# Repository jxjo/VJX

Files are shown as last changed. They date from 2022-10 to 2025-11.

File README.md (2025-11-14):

<sup>Project renamed from V-JX to VJX in December 2022 </sup>

# Project VJX
A fast glider for slopes and F3F competition. 

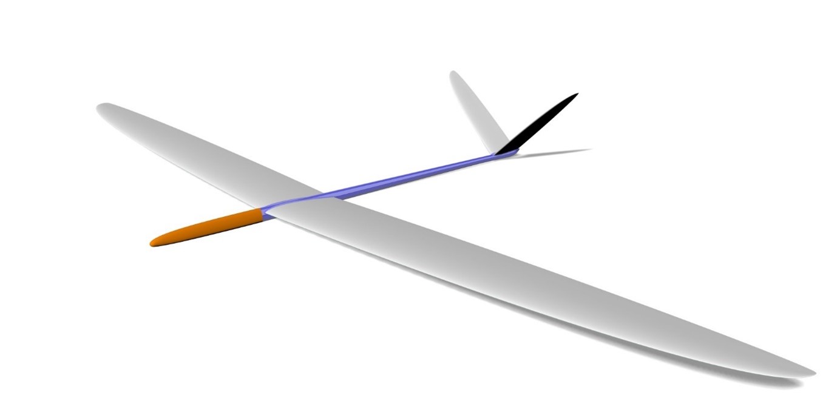
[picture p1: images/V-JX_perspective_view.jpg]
VJX VJX perspective view


VJX is a common project of Jochen Guenzel and Mario Perner where Jochen focuses on aerodynamic design and Mario on engineering and building of the model. 

Within this repository, we want to make a "full stack description" - i.e. from the aerodynamic design to the final build out of molds. As far as possible, we will make the calculations and plans available "open source" and thus also invite to a lively discussion, in which we all will hopefully be a bit smarter in the end.

#### Update 2024

A new wing, called [VJX.glide](wing.glide/README.md), is designed which complements the original VJX for medium to low conditions.

#### Update 2025

The original VJX wing has been revised and a little bit tamed to achieve better high lift capabilities. The new wing is called [VJX.race](wing.race/README.md). 

Have a look at [VJX Project Overview](#vjx-project-overview) for more information about the different developments and their current state. 

## Chapters

#### [Preliminary remarks on the procedure](#preliminary-remarks-on-the-procedure)

#### [Wing](wing/design/wing_design_1.md)
* [Design - Airfoil sections, planform, control surfaces](wing/design/wing_design_1.md) 
* [CAD](https://www.rc-network.de/threads/projekt-v-jx.11886149/post-12199653) - on RCN (de)
* [Molds and Build](https://www.rc-network.de/threads/projekt-v-jx.11886149/post-12201770) - on RCN (de)

#### [Wing VJX.glide](wing.glide/README.md)
#### [Wing VJX.race](wing.race/README.md)

####	[Tail](tail/tail_design.md)
* [Design - Tail, rudder](tail/tail_design.md) 
* [CAD and Molds](https://www.rc-network.de/threads/projekt-v-jx.11886149/post-12285083) - on RCN (de)

#### [Fuselage](fuselage/fuselage_design.md) 
* [Design - Outline, CAD](fuselage/fuselage_design.md) 
* [Molds](https://www.rc-network.de/threads/projekt-v-jx.11886149/post-12289032) - on RCN (de)

#### [Flight Experiences](#flight-experience)
#### [Project Overview](#vjx-project-overview)
#### [History](#project-history)
#### [Acknowledgement](#acknowledgements)

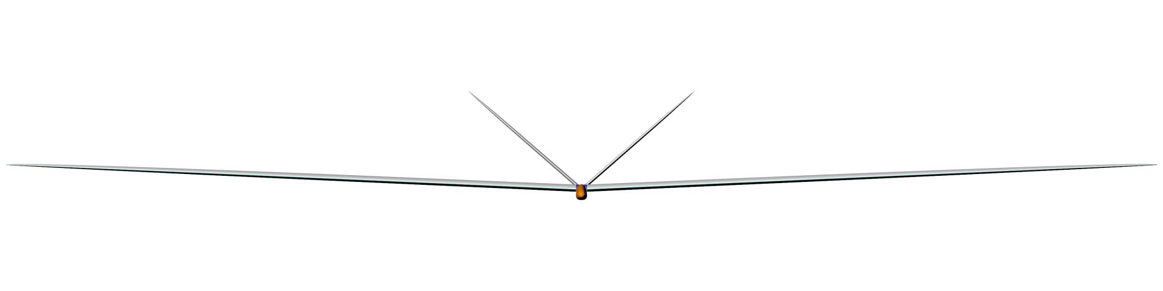
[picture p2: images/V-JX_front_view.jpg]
VJX VJX perspective view

## Preliminary remarks on the procedure

The approach with VJX is somehow atypical for the design of a new model. 

It all started with the [JX-GS airfoil family](https://github.com/jxjo/Airfoils/tree/main/JX-GS)   , which was developed specifically for F3F, but was not based on a specific model design.  In the course of time, however, thoughts matured as to what an optimal wing for this airfoil family should look like.  Which eventually resulted in a first wing design. 

Since a "proof of concept" of this wing design should be carried out as early as possible, the complete design of a new model was out of the question.   With a "test vehicle", the new wing should be put into the air as quickly as possible in order to test its performance. 

We opted for the ["Vantage"](https://ccm.in.ua/en/catalog/r-c-models/vantage/), Mario's current design for F3F/F3B.

The Vantage has perfect dimensions of a current F3F model, which makes the fuselage and tail very well suited to be equipped with a new wing module to evaluate the characteristics of VJX - also in comparison. 

In the development of a new plane, such a separate consideration of the individual components wing, tail and fuselage can be dangerous. The mutual interaction is too complex to achieve an optimized overall design. On the other hand, over the past 30 years, with countless great designs, a narrow design corridor has emerged as to what an optimal model for the F3F flight task should look like. 

Even if it may not be possible to achieve the last bit of improvement by looking at the main components separately, the procedure in the sense of "separation of concerns" of the individual components simplifies the overall development immensely.  As long as you move in the described design corridor, the probability of a "wrong design" is relatively low...

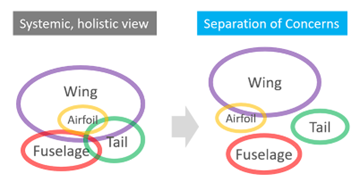
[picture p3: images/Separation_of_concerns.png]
Separation of concerns


A further aspect or guideline for the aerodynamic design, including the profile structure, was: Wherever possible and sensible, a more defensive solution with a "wide optimum" was given preference over exhaustion in a narrow area. 

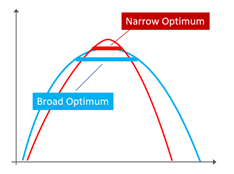
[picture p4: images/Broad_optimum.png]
Broad optimum


The danger of not hitting the "sweet spot" of a narrow optimum under competition flight conditions and thus having to accept significant performance losses far outweighs the prospect of minimal profits compared to a solution with a broad optimum.   

### Design Goals of VJX

"Pretty daring" you could say. To get involved in the round of excellent and mature F3F models such as the Freestylers, Pitbulls, Shintos, Vantage and the numerous other top models. To be even "better" in the end!

The key is certainly that there can no longer be a one-dimensional "better" in the current top models. Each model is practically unbeatable on its own. 

The difference lies in the specific characteristics of the models, which in their sum are decisive for whether a pilot controls an "optimal sports device" for him under certain conditions.

The property profile of VJX has been defined as follows with a comparative classification between o (=weak) and ooooo (=top).

|  Aspect | Score |
|---|---|
| Speed range in F3F times | |
| ... over 50s			 |ooo | 
| ... 40s – 50s			 |oooo |
| ... below 40s			 |ooooo |
| Acceleration				  |ooooo |
| Minimum curve radius		  |ooo |
| Speed in turn				  |ooooo |
| Maneuverability 			  |ooooo |
| Flight stability			  |oooo |
| Good nature 	 		  |ooooo |

Or more colloquially: "With good lift on the slope, it should be a fast, agile at the same time good-natured rocket ...".

The goal was set.  Now it's time to work!  😉

We'll start with the [Wing Design...](wing/design/wing_design_1.md) 

---

## Flight Experience

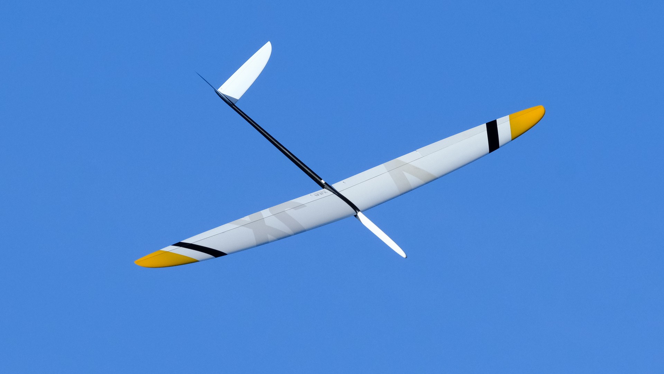
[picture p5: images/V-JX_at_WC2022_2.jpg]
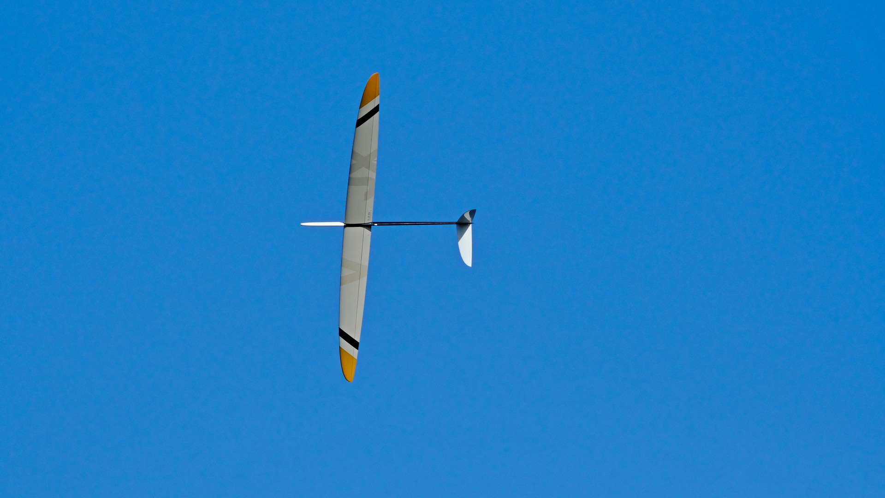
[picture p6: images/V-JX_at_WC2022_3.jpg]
 
<p align="left">
<sup>VJX prototype at F3F WC 2022 with Vantage fuselage and tail flown by Thorsten Folkers - Photos courtesy Pierre Rondel </sup>
</p>

[](https://youtu.be/vzmBOqD7ym0)
[](https://youtu.be/EWIMaU6y8Lc)
<p align="left">
<sup>VJX on a training flight and on WC round 1- Pilot Thorsten Folkers - Click to see on Youtube </sup>
</p>

First flight experiences up to now showed a very close behavior of VJX to the property profile which was defined when starting the project. 

VJX likes a wider, speed and energy oriented flight style. The faster, the better... Pilots emphasize the excellent acceleration when lift load is going towards 0 (Cl getting close to 0). 

Crucial for good flight results is the intensive use of flaps - both for the static deflection within a certain flight phase (bowling, enter course, on course) and also dynamically using snap flap to optimize for the current Cl load (curve acceleration). 
Although VJX is easy to fly being good-natured, VJX isn't "everybody darling" - it want's to be tweaked from pilots who want to get the best out of the model in regard to a certain flight style. This said, it's fascinating what Thorsten got out of VJX at F3F WC 2022 in such a short time of preparation!

## Project History 
- 2021 - June: Project start 
- 2021 - October: First prototype wing with vantage fuselage abd tail 
- 2022 - April: Flight evaluations started (brought some delay) 
- 2022 - July: Restart of flight evaluations with Tobias Reik and Thorsten Folkers
- 2022 - September: First F3F contest participation in Denmark / Sealand
- 2022 - October: F3F WC - several rounds flown by Thorsten Folkers
- 2024 - New VJX.glide for medium to low conditions
- 2025 - New VJX.race, a revision of the original VJX for medium to fast conditions  

## VJX Project Overview

The table shows the VJX family tree as of November 2025.

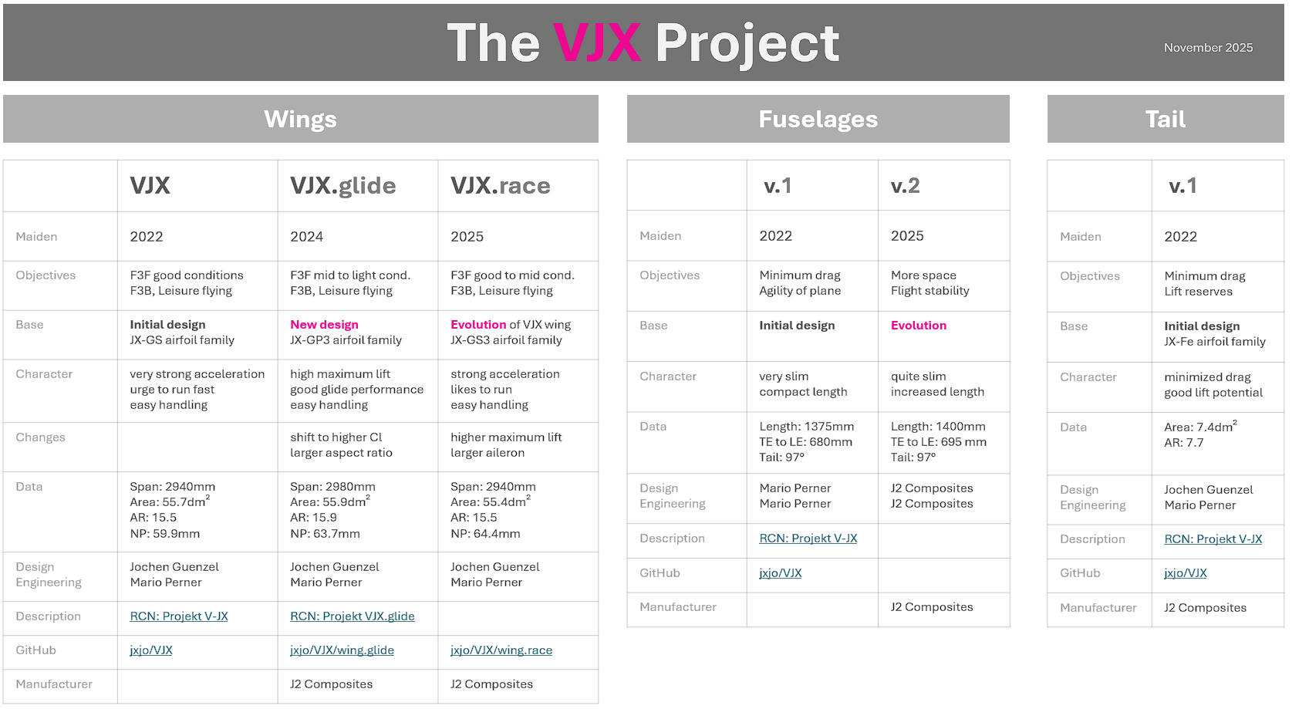
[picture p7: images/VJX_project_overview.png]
VJX Project


to be continued... 

## Acknowledgements 

What would we do without great persons and their awesome contributions?
-	Mark Drela - xfoil
-	André Deperrois - Xflr5
-	Frank Ranis - FLZ_vortex 
-	Daniel Prosser -  Xoptfoil
-	and many others... 

A special thank you to my patient punching partners Tobias Schill, Peter Wick, Matthias Boese.

Have Fun!

Jochen Guenzel & Mario Perner 

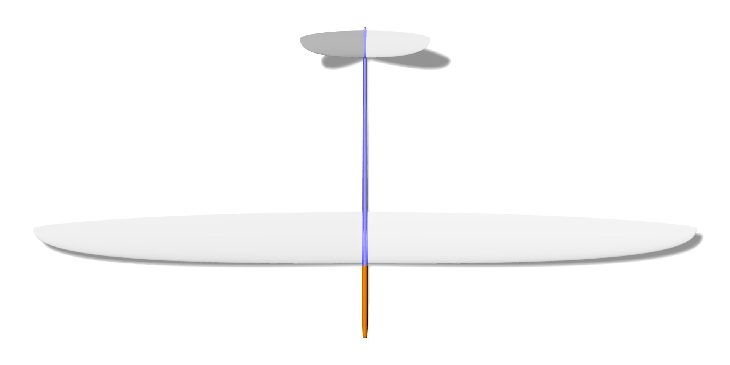
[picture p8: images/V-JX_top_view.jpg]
VJX VJX perspective view


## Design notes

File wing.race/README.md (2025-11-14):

# VJX.race

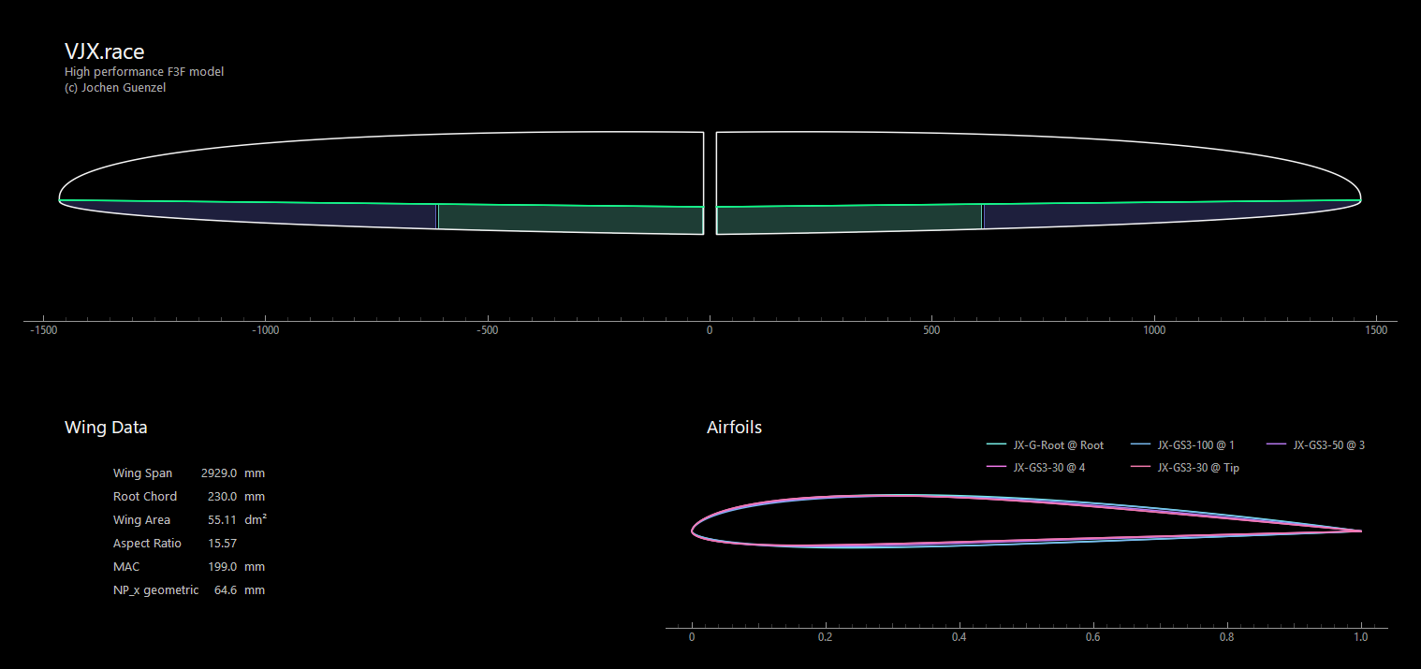
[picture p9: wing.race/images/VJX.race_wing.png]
VJX.race VJX perspective view


The VJX.race wing is a careful evolution of the original VJX. 

Based on numerous observations at competitions the design objectives for this revision were:

- Improved higher lift reserves to have more room to maneuver in tight turns.
- Enlarged ailerons with more relative width towards tip for further improved agility.
- Slightly decreased performance at Cl close to 0.0.

For the new wing, the airfoil family JX-GS was revised to achieve these characteristics. In 2025, a further refinement focused on geometric aspects resulted in the JX-GS3 family, published [on RC-Network](https://www.rc-network.de/threads/jx-gs3-strak-f%C3%BCr-sehr-schnelle-hang-segler.12079061/) and available with detailed documentation [on GitHub](https://github.com/jxjo/Airfoils/tree/main/JX-GS).

The differences between the various VJX wings can be taken from the following comparison table:

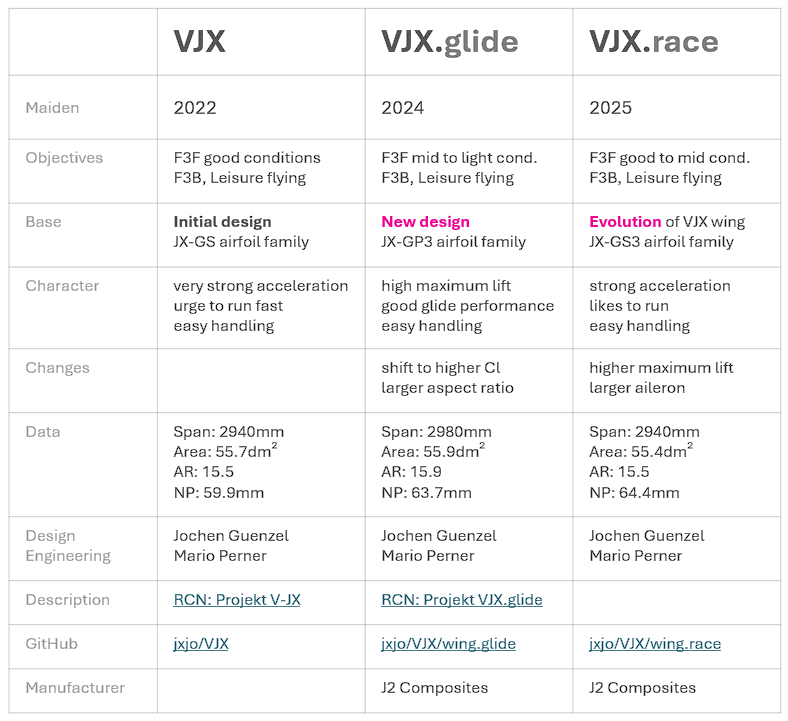
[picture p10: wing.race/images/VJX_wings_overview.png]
 

### Content of Directory 

- The airfoil family JX-GP3: `JX-GS3-100.dat`, `JX-GS3-50.dat`, `JX-GS3-30.dat`
- A root airfoil `JX-G-Root.dat` that ensures a compatible wing section at the wing root
- The [PlanformCreator2](https://github.com/jxjo/PlanformCreator2) project file `VJX.race.pc2`, which allows generation of intermediate wing sections and a draft wing planform as a DXF file
- In the subdirectory `./dxf_airfoils`, you'll find a DXF of the wing planform and all airfoils prepared with a trailing edge thickness of 0.3mm, ready for import into CAD

---
### Gallery
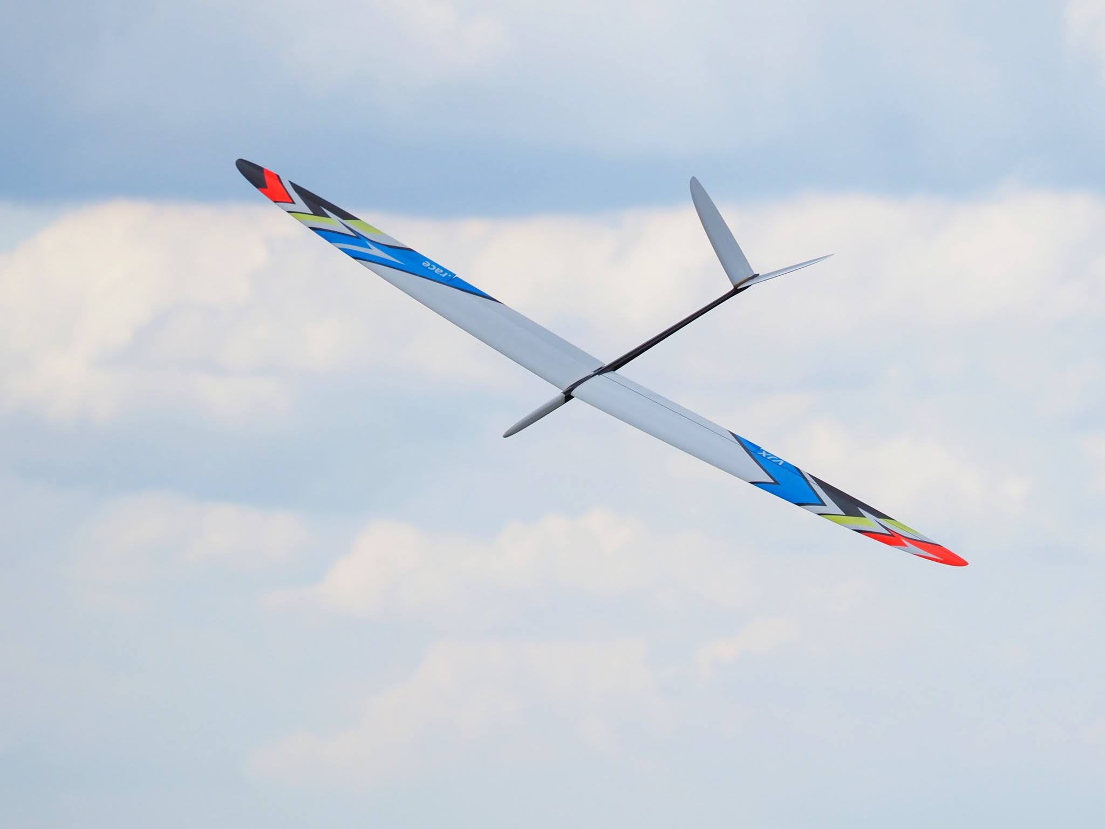
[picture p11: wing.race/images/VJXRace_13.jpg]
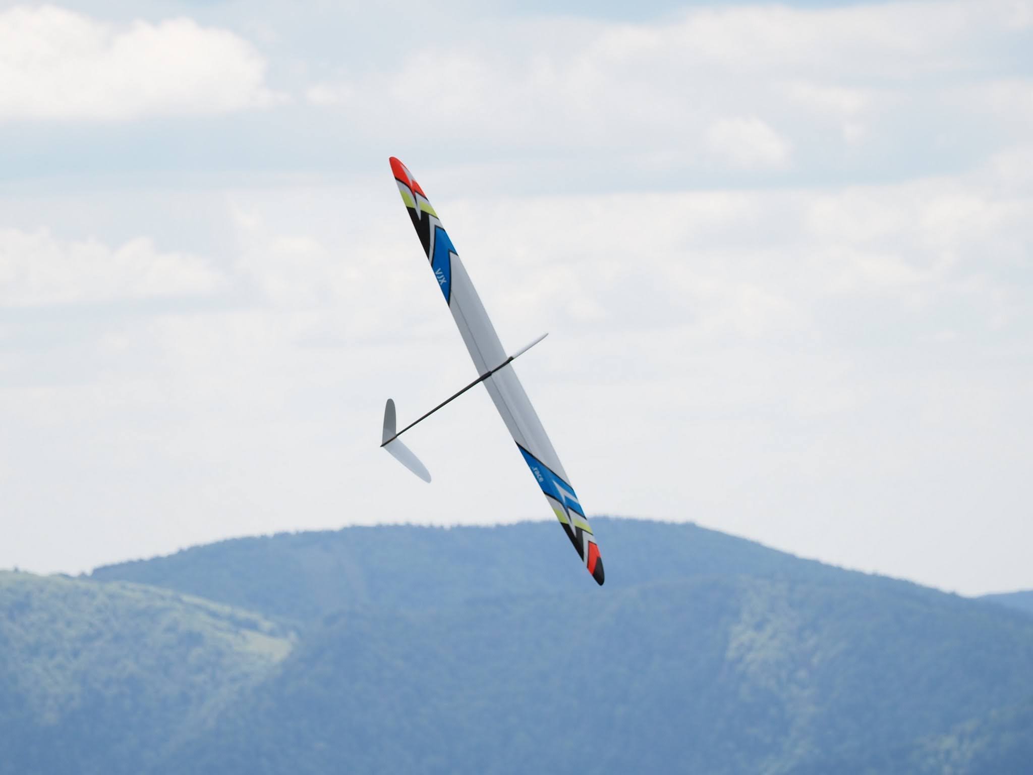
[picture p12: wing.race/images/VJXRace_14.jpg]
     
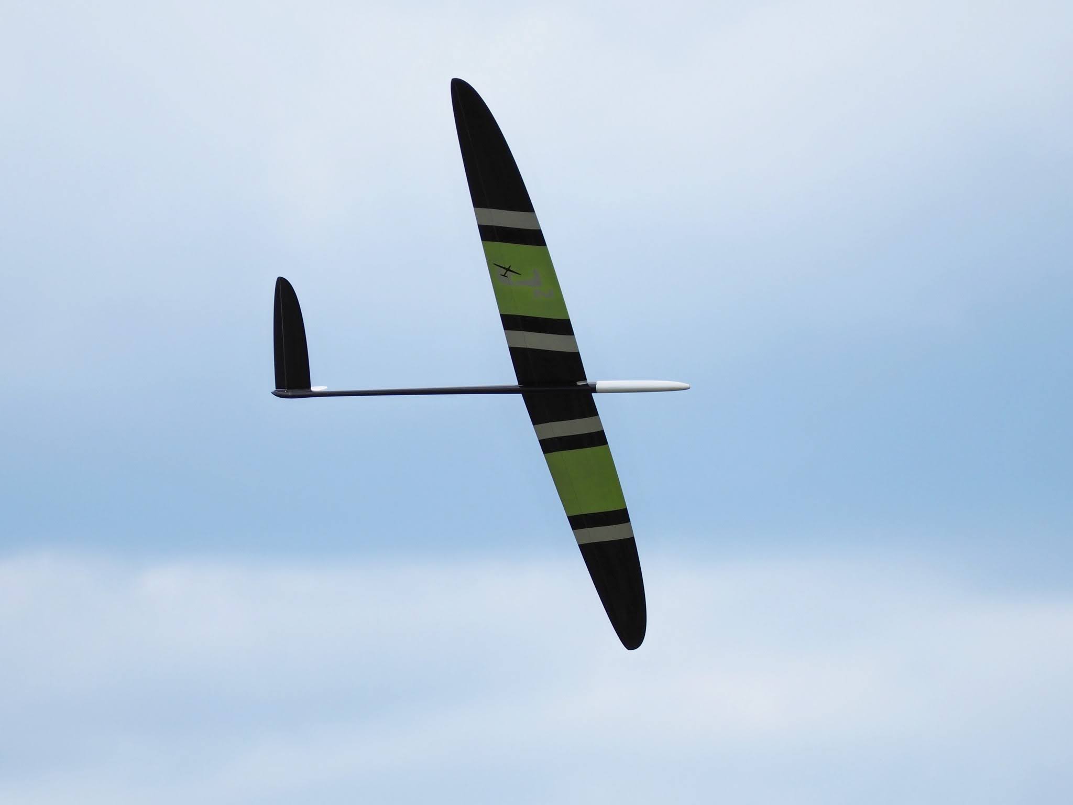
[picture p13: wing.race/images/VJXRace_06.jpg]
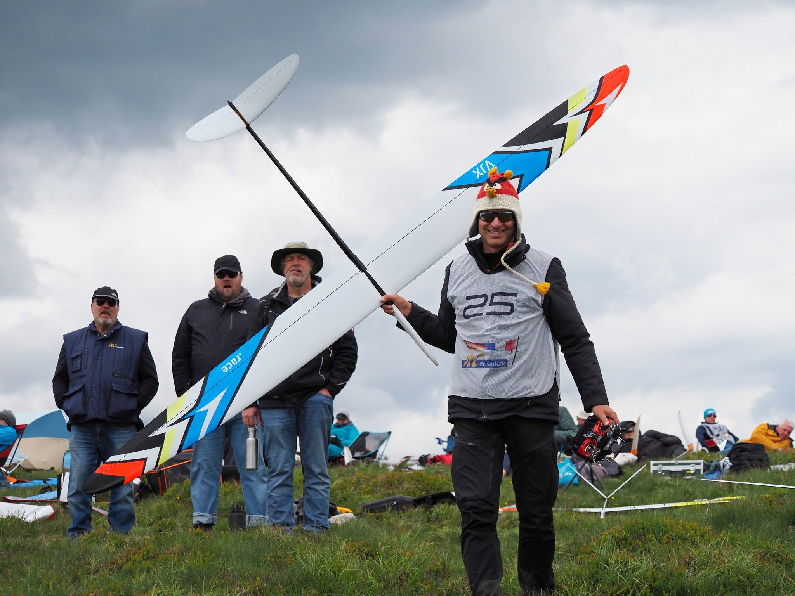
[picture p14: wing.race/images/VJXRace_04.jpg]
  
<p align="left">
<sup>VJX.race in contest - Photos courtesy of Pierre Rondel</sup>
</p>

---

Have Fun! :wink:

Jochen Guenzel<br>
2025

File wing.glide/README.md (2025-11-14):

# VJX.glide

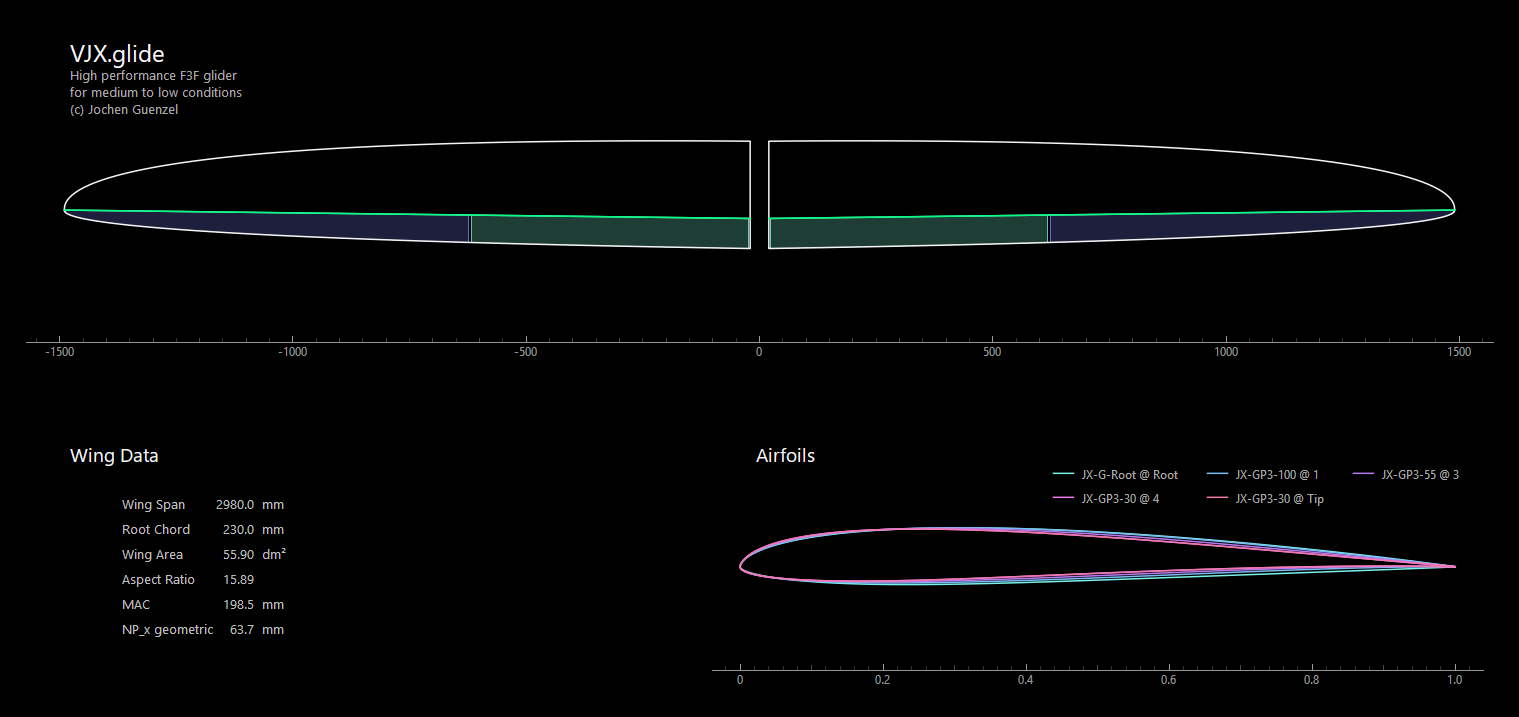
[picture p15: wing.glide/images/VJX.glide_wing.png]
VJX.glide VJX perspective view


The VJX.glide wing complements the original VJX in medium to low conditions.

Main design objectives:

- Best performance within an F3F flight time range of 45–60 seconds.
- High maximum lift reserves to allow hard, energy-efficient turns.

The differences between the various VJX wings can be taken from the following comparison table:

 

Flight reports from numerous pilots now confirm that the desired handling characteristics have been achieved exceptionally well.

A detailed description of the design considerations behind the VJX.glide can be found [on RC-Network](https://www.rc-network.de/threads/projekt-vjx-glide.11961376/).

In 2025, the original JX-GP airfoil family was completely revised and is now called JX-GP3. The updated airfoils, along with a more detailed description, are also available [on GitHub](https://github.com/jxjo/Airfoils/tree/main/JX-GP).

### Content of Directory 

- The airfoil family JX-GP3: `JX-GP3-100.dat`, `JX-GP3-55.dat`, `JX-GP3-30.dat`
- A root airfoil `JX-G-Root.dat` that ensures a compatible wing section at the wing root
- The [PlanformCreator2](https://github.com/jxjo/PlanformCreator2) project file `VJX.glide.pc2`, which allows generation of intermediate wing sections and a draft wing planform as a DXF file
- In the subdirectory `./dxf_airfoils`, you'll find a DXF of the wing planform and all airfoils prepared with a trailing edge thickness of 0.3mm, ready for import into CAD

---
### Gallery
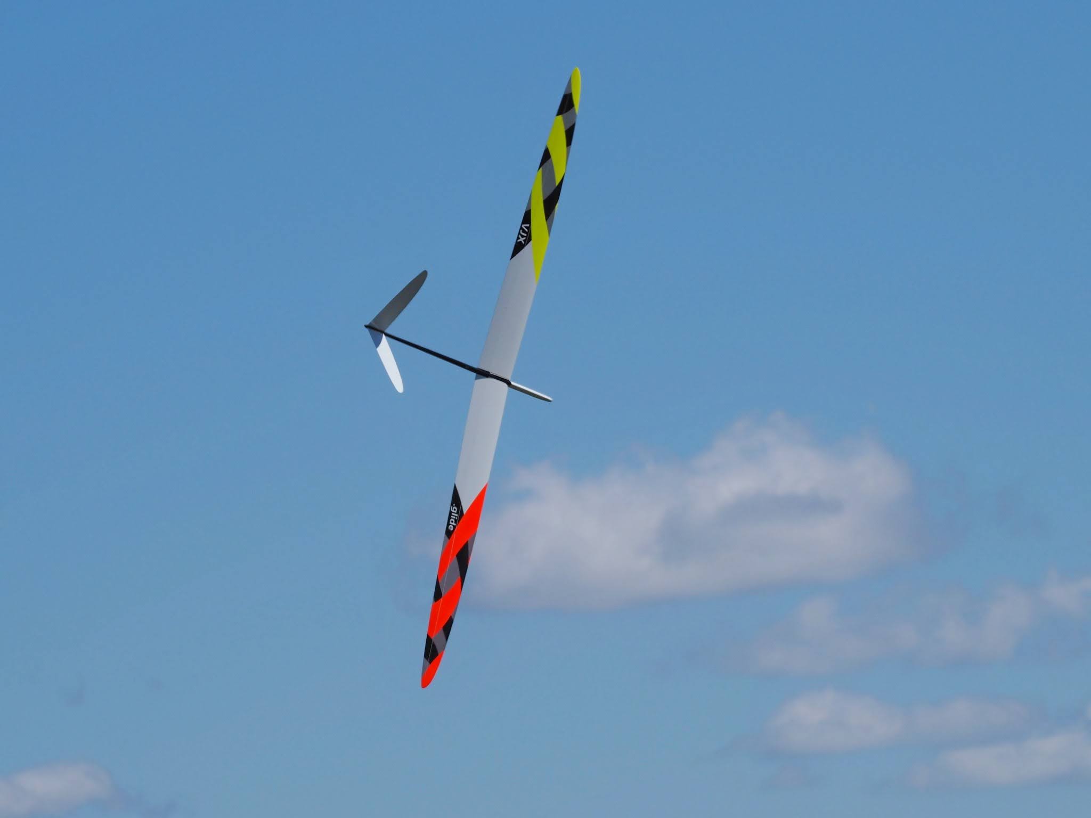
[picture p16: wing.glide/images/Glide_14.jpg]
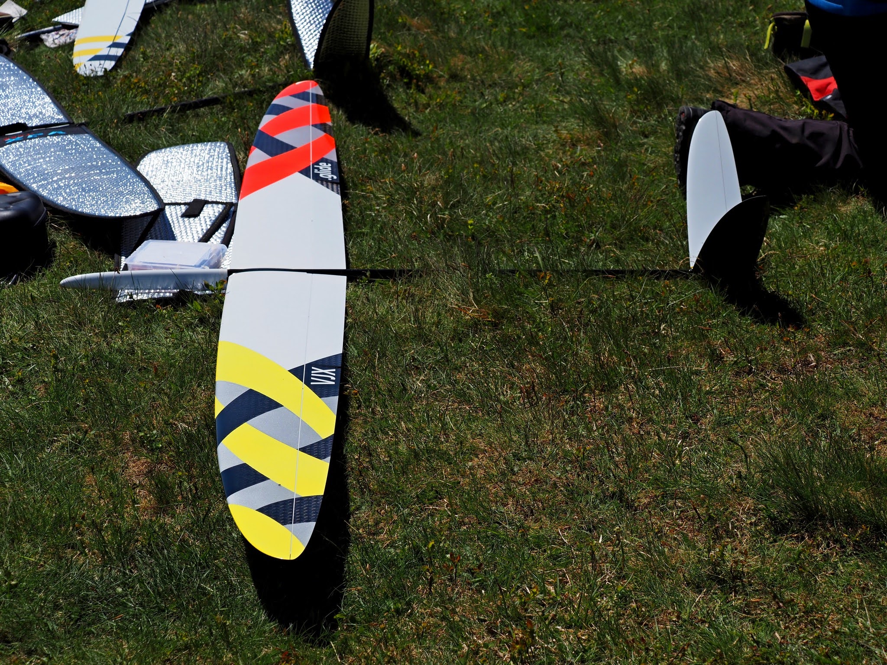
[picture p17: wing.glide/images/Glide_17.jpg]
     
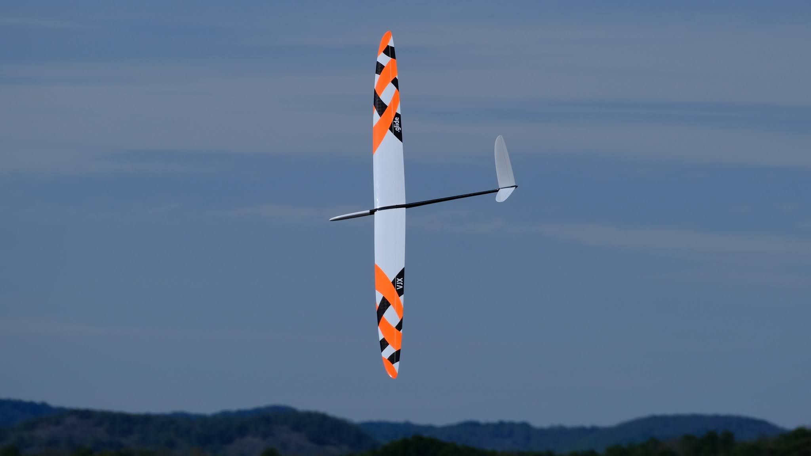
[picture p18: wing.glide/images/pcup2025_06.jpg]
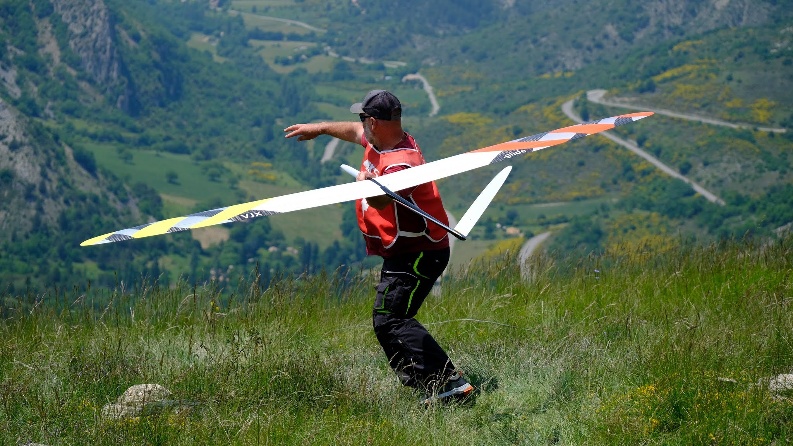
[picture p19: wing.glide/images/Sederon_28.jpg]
  
<p align="left">
<sup>VJX.glide in contest - Photos courtesy of Pierre Rondel</sup>
</p>

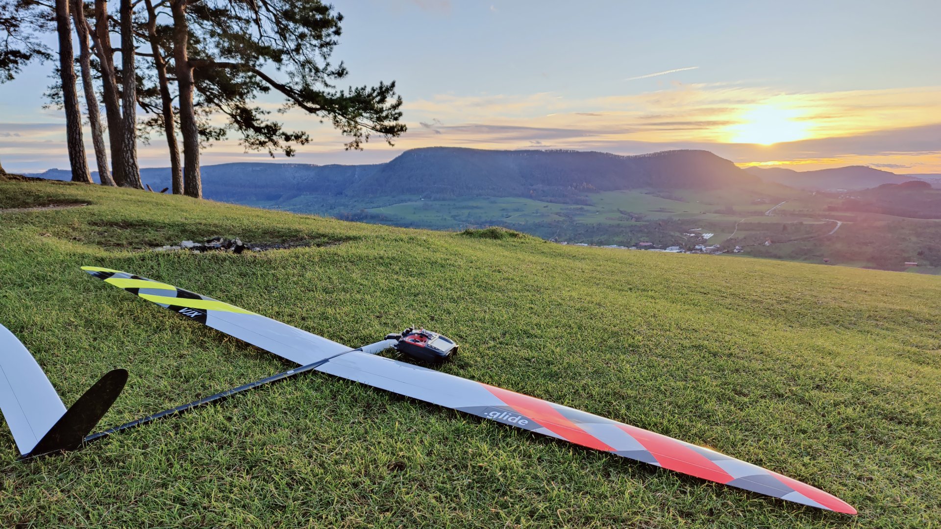
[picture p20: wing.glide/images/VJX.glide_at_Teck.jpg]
 
<p align="left">
<sup>VJX.glide waiting for clearance at Teck  - Photos courtesy of Tobi Reik</sup>
</p>

---

Have Fun! :wink:

Jochen Guenzel<br>
2025

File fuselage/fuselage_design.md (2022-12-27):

# Project VJX - Fuselage Design 

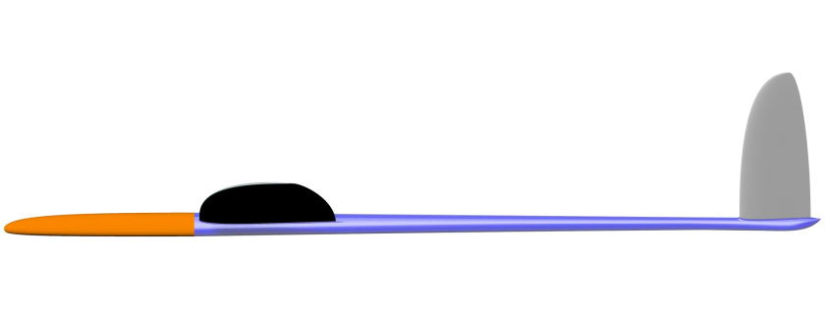
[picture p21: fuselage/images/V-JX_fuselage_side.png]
VJX Fuselage


First of all, we thought about in which direction the design of the fuselage should go. Should it become a bit more voluminous in order not to wrench the fingers too much during RC installation and perhaps also have space for a fuselage ballast? Or should it be as compact as possible to reduce the projected frontal area and also the washed surfaces? 

A thicker fuselage would have the advantage that it is easier to get it stiff enough with less material use, but a slim fuselgae looks better and should not be heavier despite more material use. By "more material input" I mean the total sum of needed fabric in g/m². 

Jochen has placed great emphasis on drag minimization in the aerodynamic design of the airfoils. In the end, we wanted to continue this with the fuselage ... 
The cross-section of the current Vantage fuselage is somewhere between Freestyler5/6 and Pitbull2 and therefore already relatively slim. So this is a good starting point for the VJX fuselage. The 12mm servo class (e.g.  KST X12 / MS320) is currently increasingly used as servos. Recently, however, there are also smaller servos from KST and MKS, which are also very well suited for the V-tail unit. I am thinking of MKS HV75k or KST HS-08. On this type of slim servos we put the focus. 
But I tried to design the height of the fuselage in such a way that the 12mm servos can still be installed. But then the boat of the fuselage must be provided with cut-outs, as with the Pitbull2. Compared to the Vantage, the VJX fuselage has now shrunk by 2mm in height, the overall width has remained the same. 
Following  the cross section of the Vantage with 42mm height at the transition hood / fuselage and the cross section of the VJX fuselage with KST X12 servos …
 
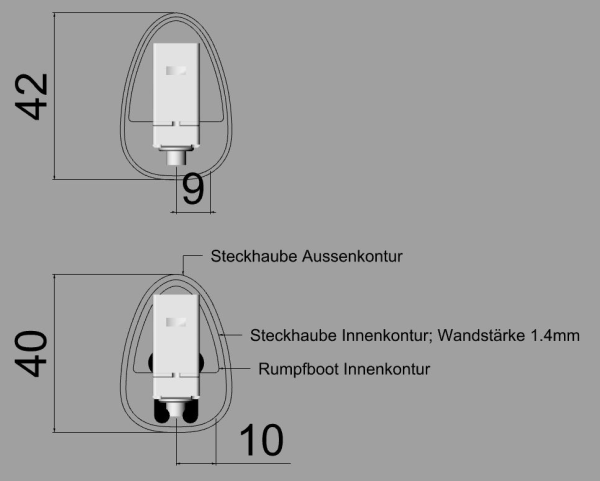
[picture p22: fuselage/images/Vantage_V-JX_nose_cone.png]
VJX Fuselage Cross Section 1


and here the VJX fuselage with KST HS-08:

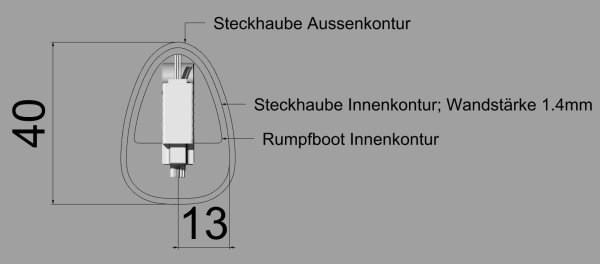
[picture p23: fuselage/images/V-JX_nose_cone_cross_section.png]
VJX Fuselage Cross Section 2

 
The wall thickness of the plug-in hood was chosen deliberately quite high, because it absorbs very high forces in unclean landings and must be built accordingly. 

The linkage of the V-tail rudders is extremely important, especially for fast F3x times. Experience shows that modern F3F models are very sensitive to elevator deflections, or in other words, they the models are flown with very little deflections. At the same time, the steering should remain stiff. A steering that is too soft or can’t be finely dosed enough will eventually become unflyable! Keep in mind that the models must be flown very (!) close to the ridge of the slope. You can help yourself here by using high-resolution  and accurate servos on the one hand, and/or by making the lever lengths on the tail rudder as long as possible. For this reason, many fuselages have this knob under the tail. Also VJX:

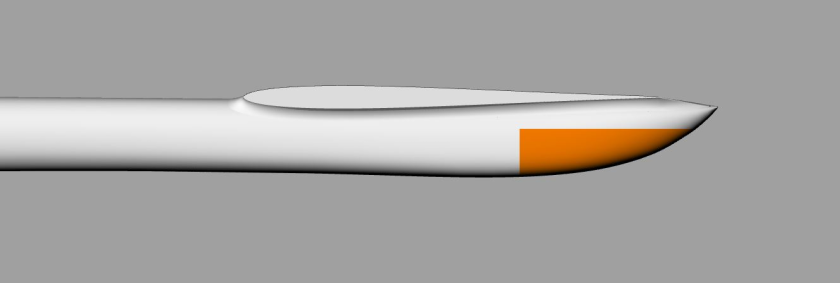
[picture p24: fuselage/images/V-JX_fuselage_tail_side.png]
VJX Fuselage Tail Bump


So, now the different dimensions would be interesting. The root chord length of the wing is already specified at 230mm. The tail has a chord length of 120mm. Exciting is the question of how long the nose the fuselage should be and how long the lever arm should be behind the wing. In my opinion there is no perfect F3f value for both the length of the nose and the length at the back, but a certain range that works by and large. 
However, since one must inevitably commit to a value, you should think about what I expect from the model. Both lengths have a strong effect on flight behavior... The longer the nose and the back lever arm tube, the more stable the model will behave around the vertical axis. For VJX, we have chosen the values a bit from the gut.

With the length of the fuselage tube we got stuck at 680mm. This is shorter than Pitbull2 and Vantage, but longer than the freestylers. 
At the front, the trend is currently towards significantly shorter noses. An extreme example is the Pitbull3 with maybe 260mm length in front of the wing. We also follow the trend, but not nearly as extremely. The VJX has a length of 320mm at the front. On the one hand, this should be short enough, for fast and tight turns and, on the other hand, in combination with the (little bit shorter) length of the fuselage at the back and the classic dimensions of the tail fine for a stable straight-line flight, especially at fast times: 

VJX Fuselage Dimensions

Whether the fuselage is visually pleasing or not, is of course a matter of personal taste. But I think it fits well into the overall low drag concept of VJX. The fact that certain restrictions in the selection of RC components are associated with this design, is in the nature of things:
 
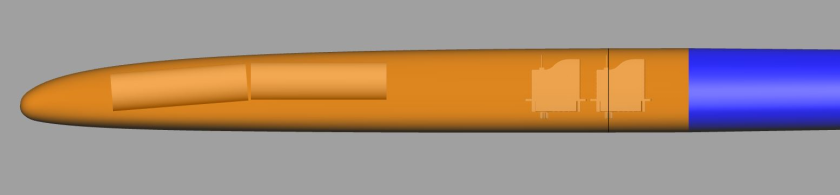
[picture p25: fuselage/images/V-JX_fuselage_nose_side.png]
VJX Fuselage Nose


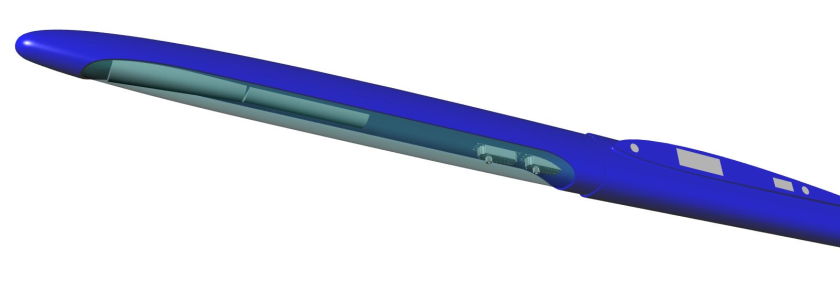
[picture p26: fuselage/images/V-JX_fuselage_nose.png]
VJX Fuselage Nose 2


VJX Fuselage
 
Mario

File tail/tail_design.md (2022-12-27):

# Project VJX - Tail Design

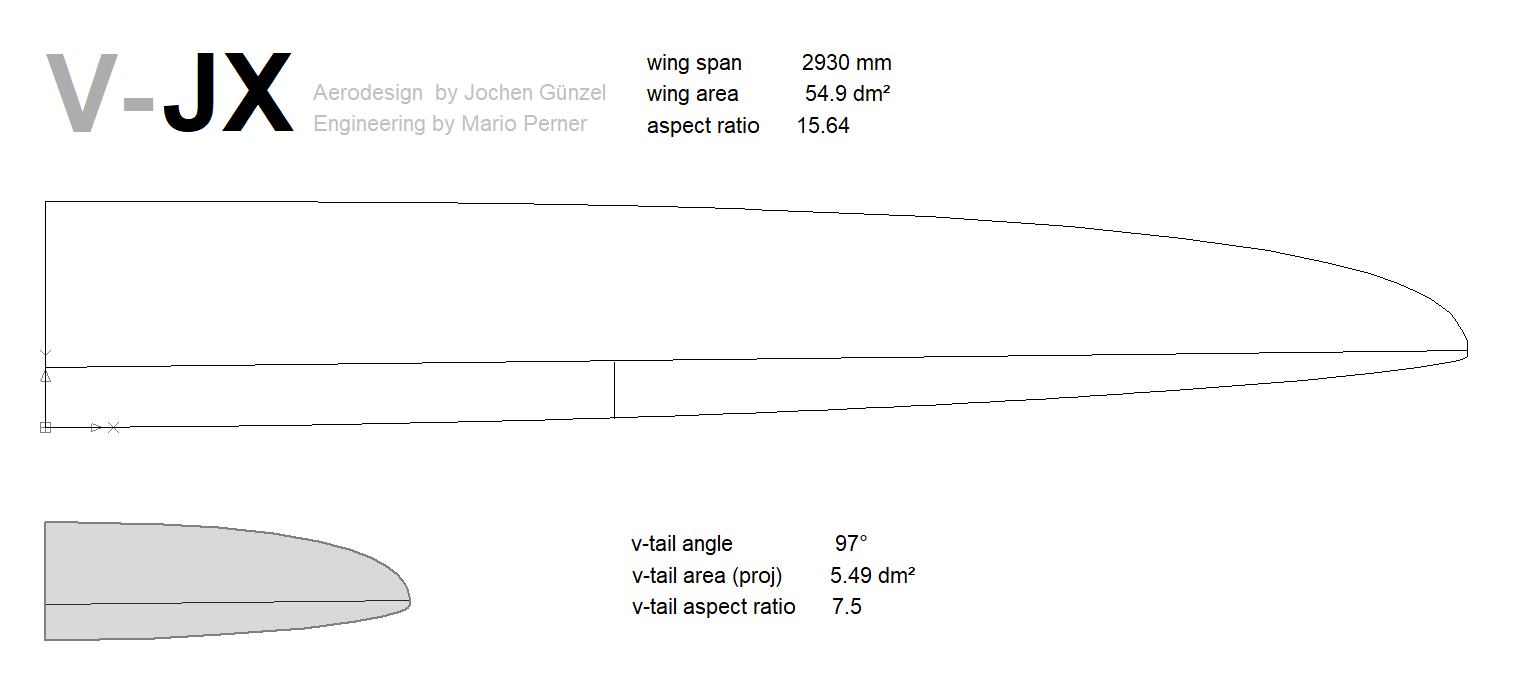
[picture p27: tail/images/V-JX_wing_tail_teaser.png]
VJX Tail Wing Layout


For the design of the tail wings, proven empirical values were largely used - i.e. initially no experiments in order not to introduce further risk variables into the overall system "VJX". 

With the rather small v-tail angle of 97 degrees, the emphasis is placed on good directional stability and damping around the vertical axis. Typically, the v-tail angle of F3F models is between 97 and 102 degrees. I was happy to follow the recommendation of Mario, who is a convinced 97 degrees fan ...

With the default value of 10% projected area to the area of the wing, this results in 5.49dm² of projected area for the tail unit. With the opening angle of 97 degrees, we get 7.31dm² of total area of the v-tail. The root chord length was set to 120mm to indirectly get a sufficient good aspect ratio (impacts induced drag). Currently all v-tails do have a root chord length between 120 and 130 mm. Like the wing, the rudder line got a small swept forward of 0.7 degrees, mainly to make the wing and tail appear to be "one piece". 

With these specifications, further artistic freedoms are already set tight limits. The further tail contour was therefore defined directly in CAD.  An optimization of the chord length distribution with FLZ_vortex was omitted, since the desired "optical shape similarity" of the wing and tail unit automatically results in a sufficiently healthy lift distribution.

### Rudder chord length

When determining the percentage rudder cord length, a weighing up or a compromise between the advantages and disadvantages of smaller or larger rudder chord length must be found. 

|  Advantages large rudder chord length | Advantages small rudder chord length |
|---|---|
| high effectiveness for small deflections | potentially longer undisturbed laminar flow |
| more height of the rudder box, easier to build, higher stiffness of the rudder |	larger deflections - less sensitive to play in the rudder linkage, smaller rudder horns |
 
The rudder chord length was finally set at a rather generous 30%. 
(A little anticipation: The fuselage will get a hump at the tail to be able to use longer rudder horns)

This completes the design of the wing plan:

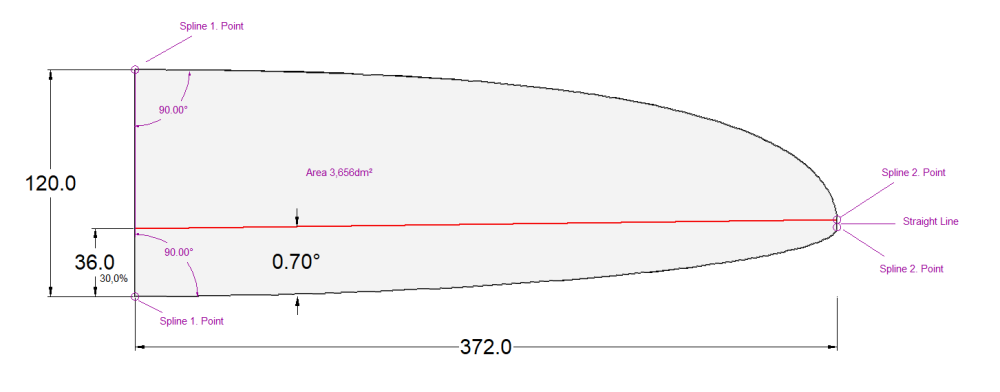
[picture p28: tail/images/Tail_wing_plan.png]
VJX Tail plan Wing Layout


## Airfoils

As part of the development of the JX-GS airfoil family, a mini airfoil family JX-Fe was also developed for the tail wing.  

The two airfoils have been optimized for use with VJX with regard to low drag between cl  0.0 – 0.4 with simultaneous robust max angle of attack.  The root airfoil has 7.2% thickness, the tip airfoil  7.0% thickness. 
 
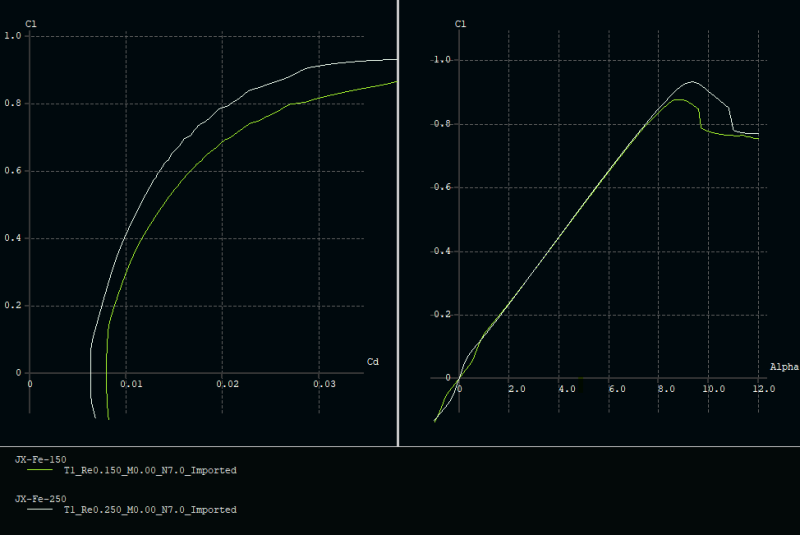
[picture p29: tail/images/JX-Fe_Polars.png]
JX-Fe Polars


Since symmetrical profiles require a "constriction" in the rear profile area for the lowest drag with decreasing re-numbers, the root airfoil benefits from its higher re-number design with a larger thickness at the rudder box (good for the linkage...).

Airfoil constriction

Both airfoils together with some polars can be found [here](https://github.com/jxjo/Airfoils/tree/main/JX-Fe).

## Xfoil/Xflr5 Special

*So that it does not remain too superficial or even boring 😉, I’d like to make a sidetrack to a little xfoil peculiarity:*

*The story started when I discovered a very small bump at cl=0.5 in the cl(cd) polar of an airfoil. Mmh. Even after changes in the alpha sequence used to calculate the polars, the small bump remained in place. The surface of the profile was perfectly smooth. That's impossible! – my curiosity was awakened …
In search of the cause, my gaze finally got stuck on the transition curve xtr bot (cl). The small bump happens just at the cl value at which the transition point at the bottom side reaches the trailing edge.  Ok. But why?
As a test, I gave the previously sharp edged airfoil a small trailing edge gap and lo and behold, the small bump was gone. That had to be the track!  But first, a little theory:*

*In the xfoil calculation of the circulation (-> lift), the trailing edge is of particular importance. There, the Kutta condition applies:*

The sharp trailing edge of a wing is not flown around, but the adjacent flow flows smoothly there. In an adjacent flow over a two-dimensional body with a sharp trailing edge, a circulation builds up that is just large enough that the rear stagnation point is at the trailing edge. 

*Important in this context is the phrase "sharp trailing edge".  In the case of a trailing edge gap, Xfoil inserts an additional panel to close this gap and also to meet the condition of a closed airfoil. Obviously, this blunt trailing edge leads to a modified algorithm for calculating the circulation and also to the tricky question of how different states laminar-turbulent on the top and bottom at the trailing edge are merged.*

*And indeed: In the Xfoil routine on the influence of the TE (trailing edge) you will also find this line of code:*

	`SHARP = DSTE  .LT.  0.0001 * CHORD`

*i.e. Xfoil treats all trailing edge gaps < 0.01% as "sharp" – larger gaps are "blunt". In the case of "blunt", a vortex strength is applied to the final panel, which then influences the overall circulation of the airfoil. The differences are negligible in normal profile calculations – except*

-	*in the calculation of the moment coefficient cm, where the changed pressure distribution at the trailing edge due to the long lever arm has a strong influence on cm  (important for  the evaluation of wing-only airfoils).*
-	*in the case of symmetrical profiles and lower re-numbers, where detachment bubbles at the trailing edge cheerfully move between the top and bottom and contribute to the "dead band effect".  The effects become much smaller with a small trailing edge gap.*

*As a former protagonist of a sharp trailing edge, I am now remorsefully purified and now set the "TE gap" to a safe 0.03% in all my airfoil  calculations and comparisons. Well, nature has it much easier here. It simply lets the air flow over the trailing edge as if there were nothing there. If she knew how complicated it actually is...* 😉

### Tail design completed 

This completes the design of the tail and all data is ready for 3D CAD.

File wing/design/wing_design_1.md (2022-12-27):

# Project VJX - Wing Design Part 1

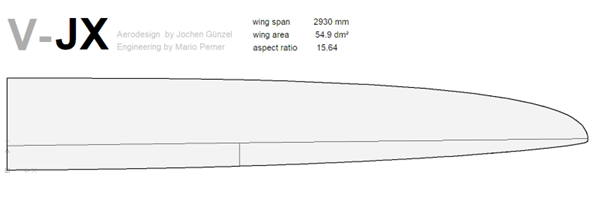
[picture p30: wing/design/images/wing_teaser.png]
VJX Wing Layout


## Key design data of the wing 

Since the wing should first be evaluated with a Vantage fuselage, the chord length at the root is specified as 230mm, which is also a good average. Practically all current F3F models are in a range between 225 - 235mm at root.

Maneuverability is one of the important design goals, the half-span was set at 1450mm - with fuselage this results in a total span of approx. 2930mm. This value is rather at the lower end in comparison to most of the current F3F models..

(*Off topic: Perhaps even more important in setting the wingspan was that the wing just fits into the trunk without moving the passenger seat*) 

Wing area and thus aspect ratio will result from the determination of the chord length distribution along wingspan in one of the next steps.

## Airfoil family JX-GS

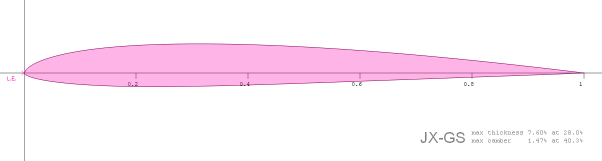
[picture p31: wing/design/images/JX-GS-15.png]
JX-GS-15


All the airfoils of the wing can be found [here](https://github.com/jxjo/Airfoils/tree/main/JX-GS). Development of the JX-GS airfoil family (in Geram we use the term "Strak") was done in several iterations and was described in detail in [Entwicklung eines F3F-Profils]( https://www.rc-network.de/threads/entwicklung-eines-f3f-profils.787618/). This thread on RC-Network has also become a great fund for questions about airfoil development due to the numerous discussion contributions.

Therefore, at this point only a short summary of JX-GS:

-	Fast slope airfoil - especially for F3F
-	Design objective: "Robustness" in turbulent flow conditions on the slope
-	Pronounced flap airfoil with low camber: speed position at 0 degrees, fast gliding with 0.5 - 1 degree flap position
-	The airfoils are "synthetic" - they were created by [Xopfoil-JX](https://github.com/jxjo/Xoptfoil-JX/releases) without a human touch on the airfoil surface

The name of the individual airfoils gives an indication of their optimal conditions of use within the wingspan - see [here](https://github.com/jxjo/Airfoils/blob/main/JX-GS/readme.md). 
Drawing the individual airfoils with their optimal chord length, shows the wide range of chord this airfoil family covers at a wing:

JX-GS Strak

## next: [Wing Design Part 2](wing_design_2.md)

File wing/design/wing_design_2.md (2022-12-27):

# Project VJX - Wing Design Part 2

## Wingplan - chord length distribution

Beside airfoil characteristics, the chord depth distribution along the wingspan has the greatest influence on the properties of the wing. It determines decisively 

-	lift distribution and thus the induced drag, especially at higher lift coefficients 
-	lift safety margin in the outer wing for good-natured behaviour at flight limits

Unfortunately, both properties are in competition, so it is important to find an optimum according to the requirements profile. Since finding this individual optimum is probably the most important design task in wing design, it will be discussed in more detail below.

## Induced drag - elliptical lift distribution 

Since the induced drag grows square to the lift coefficient, it affects particularly the total drag of the wing at high lift values. In the F3F flight task, this is the short but crucial section of the turn, which is typically flown with a Cl between 0.6 and 0.8 (see also the results of [real flight measurements](https://www.rc-network.de/threads/flugvermessung-bei-f3f.11812891/post-12099993) - sorry in German). 

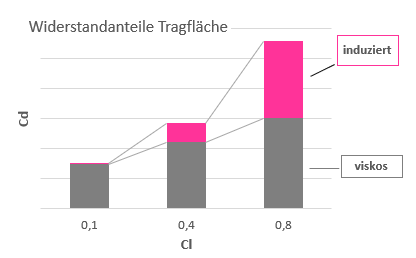
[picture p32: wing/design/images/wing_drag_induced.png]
Induced drag


If the induced drag (and thus the total drag) in the turns should be reduced as an optimization goal, our wing should have an elliptical lift distribution, which corresponds to an elliptical chord length distribution in first approximation. 

How much would be the improvement of such an optimization in terms of induced drag? 

The graph compares two wings, one with elliptical and one with "quite elliptical" (= slightly super elliptical) chord length distribution, such as VJX. 

Elliptical vs. VJX

The calculated possible improvement of a strictly elliptical chord length distribution of 1.0% at Cl=0.8 is quite a typical value. We should keep this value in mind when it comes to discussing the necessary lift reserves in the outer wing later.

The slightly improved drag of the super elliptical wing at low Cl values is remarkable. Without further examinations, I suspect the higher Re numbers and thus lower airfoil cd values for a "fuller" super relliptical wing are the reason for this effect.

## What to do with the outermost wing tip?

Before we turn to the lift distribution and the lift reserves, a brief consideration of the outermost wing tip, i.e. the last 2-5 centimeters of the wing. 

For a long time I struggled with the typical "artifacts" of lift and drag values at the wing tip ... 

Wing tip artefacts

... and tried unsuccessfully to master them. At the tip of the wing it becomes somehow special:

-	due to the very low chord length, the Re number goes well below 50,000. In this area of low re-numbers, the calculation methods implemented in Xflr5 or Flz_vortex are increasingly failing. The calculated results are very "questionable".
-	Due to the pressure compensating flow between the bottom and top surface, 3-dimensional effects (cross flow) come into play, which cannot be covered by our simple calculation methods.

So, what to do? I choose the simplest solution: "Ignore! That will work...". In the following considerations, the last centimeters of the wing are left out. The shape of the outer tip will be shaped only from a purely esthetic point of view. 

## Chord length distribution - lift and lift reserves 

After considering the drag of the wing, it is now time for the lift distribution along the wing. Two main objectives are pursued:

1.	A uniform, constant course of the local lift coefficient with a slight increase towards the middle of the wing
2.	Stall at high angles of attack should happen first towards root of the wing to avoid uncontrolled "Abschmieren" (German phrase). Conversely, the last third of the wingspan should have certain lift reserves. 

The local lift coefficient and local max angle of attack influenced by

-	the airfoil ... 
-	the local chord length and thus the Re number 
-	the effective local angle of attack as the sum of the angle of attack of the wing and induced angle of attack at this section (which is negative) 
 
Regarding the above influence of the airfoil, a short bridge to the airfoil family ("Strak") should be made: A good strak is characterized, among other things, by the fact that the airfoils towards wing tip, i.e. with a smaller re-number, can go along with their the alpha the inner airfoils:

Tip airfoil at lower Re number
 
Equipped in this way, we go to work in Flz_vortex, which is better suited than Xflr5 for this work step. It starts with the basic dimensions, root chord length and wingspan, and an elliptical chord length distribution...

My approach to the wing design with Flz_vortex is 

-	straight, horizontal trailing edge (reference line for swept is 100% chord) 
-	not too many (effort!), not too few (accuracy!) wing segments. Width of segments decreasing to the wing tip
-	the inner 2 segments are as wide as the (considered later) flap
-	the right half wing is the reference wing (e.g. elliptical chord length distribution), the left half wing is then iterated and optimized
-	the calculated curve of induced drag is ideal for creating a continuous outline because it is sensitive to changes in the chord length gradient
-	When the changes made to the chord length become smaller then +-0.5mm, iteration is finished. 

After a few iterations, the preliminary interim result is ready. An idealized wing with the desired lift distribution, slightly super elliptical and with slightly increased induced drag (about 1% at Cl=0.9 - see view above) compared to an elliptical wing planform. 

Lift distribution

Interim conclusion: The base design of the cord length distribution is relatively "sharp" with only a few lift reserves in the outer wing. Regarding lift reserves, however, an adapted flap depth should give an extra push... More on that later. 

In the next part, we first compare the chord length distribution of VJX with other, current F3F models and then take a closer look at the rudder depth distribution along wingspan. 

## next: [Wing Design Part 3](wing_design_3.md)

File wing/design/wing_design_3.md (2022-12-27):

# Project VJX - Wing Design Part 3

## Chord length distribution - Verification 

So far, a lot has been calculated, iterated and also some assumptions were made. But where do we stand with our draft? Are we on the right track? 

One of the few ways to answer these questions is to check whether the current design is in the design corridor of successful F3F models described above. If so, we can at least assume with some certainty that we are not entirely wrong...

For this purpose, the depth distribution of some current F3F models was measured from the published side views and scaled to the wingspan and root chord length of VJX. 

Comparsion chord length

<sub>Comparison of the normalized **approximate** chord length distribution of current F3F models. The edges of the design corridor form Quantum, with almost elliptical chord length distribution and Pitbull 2 with strong pronounced super elliptical distribution.</sub>

Conclusion of the verification: That fits. Keep it up!

Based on the chord length distribution found, it can now go to the last important design step: 

## Rudder chord length distribution

As a pronounced flap airfoil, the JX-GS "lives" on the use of the flaps. That means, flaps are always more or less deflected - except perhaps for a short period time on a high speed straight line course. Even if it's almost trivial, first a list of the tasks or requirements for the "flap concert" of the (inner) flap and (outer) ailerons in order to keep an eye on the various aspects.

1.	Static adaptation of the wing polars to the flight conditions: Up to mediumn conditions  , both flaps should be uniformly positively deflected (0.5 to 2 degrees). In very good conditions, the flaps are in the zero position.
2.	Improvement of the high-lift properties in the turns by use of snap flap. 
3.	Good to very good maneuverability around the longitudinal axis due to well sized ailerons
4.	Very good effect of the flaps for landing - butterfly setting
5.	Improvement of the lift reserves in the outer wing at high Cl values by geometric twist with a reduced rudder chord length 

In doing so, the basic consideration must be made:

-	large rudder chord length, high impact, smaller deflections, lower drag increase
vs.
-	smaller rudder chord length, no early disruption of the laminar flow by the rudder gap

In consideration of the aspects, the rudder chord length at the root was set at 26.5%. Comparable F3F models are in a range of 25% - 28%.

Trickier is the question of whether the rudder chord length should taper along wingspan or remain constant? A decreased rudder chord length results in a geometric twist that leads to a changed lift distribution (see chapter above "Chord length distribution - lift and lift reserves")

Since "good-naturedness" - here avoiding tip stall during fast flown turns - is one of the important design goals, a slightly decreasing rudder depth towards wing tip was finally defined. 

In Flz_vortex, the effect of a decreasing rudder chord length can be well visualized:

Decreasing rudder chord length

## Swept rudder hinge line

The rudder or hinge line is the only straight reference line of the wing. With the defined section and rudder chord length distributions, the shape of the wing is already geometrically determined. 

The angle of the rudder line determines sweep back of the wing where the rudder line is the reference line. The 0-degree hinge line used in many F3F models results in a remarkable sweep back of the wing...

Sweep back in comparsion
 
... which in turn results in more torsional load on the wing (ideally, the quarter chord line should be straight and horizontal). For this reason, the hinge line was slightly moved forward by 0.7 degrees.  

*The second reason: It just looks prettier to me!
Whether such small swepts of the rudder line have a significant influence on flight mechanics could not be researched so far. The majority of the current F3F models have a 0-degree hinge line.  On the other hand, "Orden" and especially "Shinto" have a clear "swept forward" of 1.5 and 2 degrees respectively. There seems to be a slight tendency.* 

In the [data subdirectory](data) you'll the FLZ_vortex project file with the comparison of VJX to an elliptical wing.

In the 4th and final part of the wing design, we take a look at the performance of the wing in Xflr5 in order to finally determine the wing plan including the position of the airfoil sections. 

## next: [Wing Design Part 4](wing_design_4.md)

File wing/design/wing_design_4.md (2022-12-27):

# Project VJX - Wing Design Part 4

## Wing aerodynamic calculation with Xflr5

Actually, we would now have all the data to define the wing in Xflr5 and perform an aerodynamic calculation. Unfortunately, Xflr5 cannot automatically determine the intermediate sections resulting from the segmentation of the wing. Therefore, a decision has to be made between 

1.	A very simplified wing with only 3 trapezoidal segments for the 4 existing profiles of the airfoil family. However, this results in a high deviation from the previously elaborated chord length distribution within the sections ...
2.	Define more wing segments and distribute the 4 airfoils as well as possible. This is better or more accurate than variant 1 - but may not do justice to the airfoils.
3.	Define more segments and calculate the additional necessary intermediate airfoils.

We opt for variant 3. However, this can hardly last long without machine support. The manual click effort quickly becomes very high, especially if the wing should be calculated with deflected flaps or other airfoil variants.

*Often you get to the point where you say, "I don't care anymore - this wing will fly somehow!" In such a situation only a soothing cup of tea may help...*

Fortunately, there is the small tool Xfoil_Worker which is part of the [Xoptfoil-JX package](https://github.com/jxjo/Xoptfoil-JX/releases) which allows, packed in a batch job, to automate some work steps: 

-	Creating intermediate airfoils by blending two basic airfoils
-	Setting flap on an airfoil - for simplicity, however, a constant flap chord length of 25% has now been defined
-	Create the necessary Xfoil polar sets for all airfoils used in the wing.   
 
Both the generated airfoils and all associated polars can then be read into Xflr5 in one go, so the wing analysis can then be started directly afterwards.

A note on the mixing or blending of two similar airfoils to create a new intermediate airfoil: It is astonishing - or not - how geometric mixing also "mixes" the aerodynamic properties of the two profiles in the same proportion. Nice.

Finally, the wing appears on the screen in all its beauty ...

VJX Xflr5Wing

... and the calculations can start. Important: Since only the wing has been modeled so far, the results are only suitable for qualitative or comparative studies, such as the effect of different chord length distributions. If the wing area of a variant changes, the weight must be readjusted in order to keep the wing load of the wing variants constant. 

In this brief design description, an analysis and discussion of different polars and key figures along wing span is omitted. You'll find the Xflr5 project file in the data subdirectory.

## Final 2D wing plan

The design work has now been completed. With the 2D wing plan, the final "look" of the wing is defined in this last design step.

It would be nice if the wing could have a certain individual look compared to the common designs and of course also finds favor in the eyes - at least - of the designer.

Artistic freedom in outline design is subject to very narrow limits due to the specifications that have already been made:

-	Chord length distribution
-	Rudder chord length distribution
-	Swept angle of the hinge line
 
In addition, the curvature of the wing outline should be as steady as possible in order to avoid artifacts in the subsequent 3D-design.

First, the wing segment geometries are transferred from Flz-vortex to 2D CAD. Splines are then used to try to form a wing outline that comes as close as possible to the segment geometry. For a harmonious curve progression, the splines should have as few control points as possible. Therefore, the splines have only 2 control points which define slope and curvature of the spline.  The wing tip gets its final shape with an additional, helper spline. 

After this optical fine tuning, the rudder chord length no longer decreases linearly from the root to the wing tip, but is practically constant up to the aileron and then decreases to the wing tip. 

Wing planoutline
   
Now only the airfoils are missing. 

For 3D design, it is recommended to work with a few additional airfoil sections to ensure that "overlaying" the surface in 3D does not lead to geometric distortions of our airfoil strak. For the wing root, the basic profile JX-GS-15 was slightly thickened to 7.9% to support statics and to become a little more variable in terms of wing connector height:

Wing airfoils

Ok! Everything should be ready for 3D CAD design ...

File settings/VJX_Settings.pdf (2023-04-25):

# VJX Settings

CG - Center of Gravity

Ballast

Deflections

Camber

Snap Flap

Finally


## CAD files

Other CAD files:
tail/data/V-JX_tail_plan.dxf
wing.glide/dxf_airfoils/VJX.glide_wing.dxf
wing.race/dxf_airfoils/VJX.race_wing.dxf

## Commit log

2022-10-04 Wing Design 1
2022-10-04 Wing design 2
2022-10-05 Wing design 3
2022-10-05 Wing design 4
2022-10-06 Add v-tail plan
    [V-JX_tail_plan.dxf]
2022-10-07 Fuselage Design added
2025-11-13 updating VJX.glide
    [VJX.glide_wing.dxf, VJX.race_wing.dxf]
